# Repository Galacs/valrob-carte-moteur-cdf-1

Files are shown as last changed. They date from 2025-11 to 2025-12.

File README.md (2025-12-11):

# Carte moteur CDF 1

ESP32-S3-WROOM-1 Dual 5A DC motor driver

## IC List

- ESP32-S3-WROOM-1 (Main MCU Module)
- AP2112K (MCU 3v3 LDO)
- DRV8874 (Integrated FETs H-bridge)

## Top preview



## Preview 3d render



## Pin definitions

```c
#define EN_1_PIN 2
#define PH_1_PIN 3
#define SLEEP_1_PIN 5
#define FAULT_1_PIN 6
#define IPROPRI_1_PIN 7

#define EN_2_PIN 14
#define PH_2_PIN 17
#define SLEEP_2_PIN 21
#define FAULT_2_PIN 38
#define IPROPRI_2_PIN 18

#define SPI_CS_0_PIN 10
#define SPI_CS_1_PIN 8
#define SPI_MOSI_PIN 11
#define SPI_MISO_PIN 13
#define SPI_SCLK_PIN 12

#define ALERT_1_PIN 47
#define ALERT_2_PIN 48

#define BATT_SENSE_PIN 9
```

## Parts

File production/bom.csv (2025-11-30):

Designator | Footprint | Quantity | Value | LCSC Part #
_2, |  | 2
C1, C2, C5 | 0603 | 3 | 1u | C15849
C10, C13, C14, C4, C7, C9 | 0603 | 6 | 0u1 | C14663
C11, C15 | CP_Elec_6.3x7.7 | 2 | 220u | C46550411
C12, C8 | 0603 | 2 | 22n | C21122
C3 | 0603 | 1 | 10u | C19702
C6 | 0805 | 1 | 22u | C45783
D1, D16 | D_SMA | 2 | D_Schottky | C22452
D10, D11, D12, D13, D14, D15, D17, D18, D19, D6, D7, D8, D9 | Diode_DFN1006 | 13 | H5VU10U | C22395519
D2 | 0805 | 1 | GREEN | C2297
D3 | D_SMB | 1 | P6SMB6.8CA/TR13 | C78395
D4 | D_SOD-123 | 1 | BZT52B3V3 | C19077392
D5 | D_SMA | 1 | SMAJ12A | C19077531
J1 | USB_C_Receptacle_HRO_TYPE-C-31-M-12 | 1 | USB_C_Receptacle_USB2.0_14P | C393939
R1, R10, R15, R2, R3 | 0603 | 5 | 5k1 | C23186
R11, R16 | 0805 | 2 | 16k | C17490
R12, R17 | 0603 | 2 | 1k | C21190
R13, R18, R5, R6, R7 | 0603 | 5 | 10k | C25804
R14, R19 | 0603 | 2 | 20k | C4184
R4 | 0603 | 1 | 3k3 | C22978
R8, R9 | 0603 | 2 | 22 | C23345
SW1, SW2 | SW_SPST_TS-1088-xR020 | 2 | SW_Push | C720477
U1 | SOT-23-5 | 1 | AP2112K-3.3 | C51118
U4, U5 | HTSSOP-16-1EP_4.4x5mm_P0.65mm_EP3.4x5mm_Mask2.46x2.31mm_ThermalVias | 2 | DRV8874 | C1855818

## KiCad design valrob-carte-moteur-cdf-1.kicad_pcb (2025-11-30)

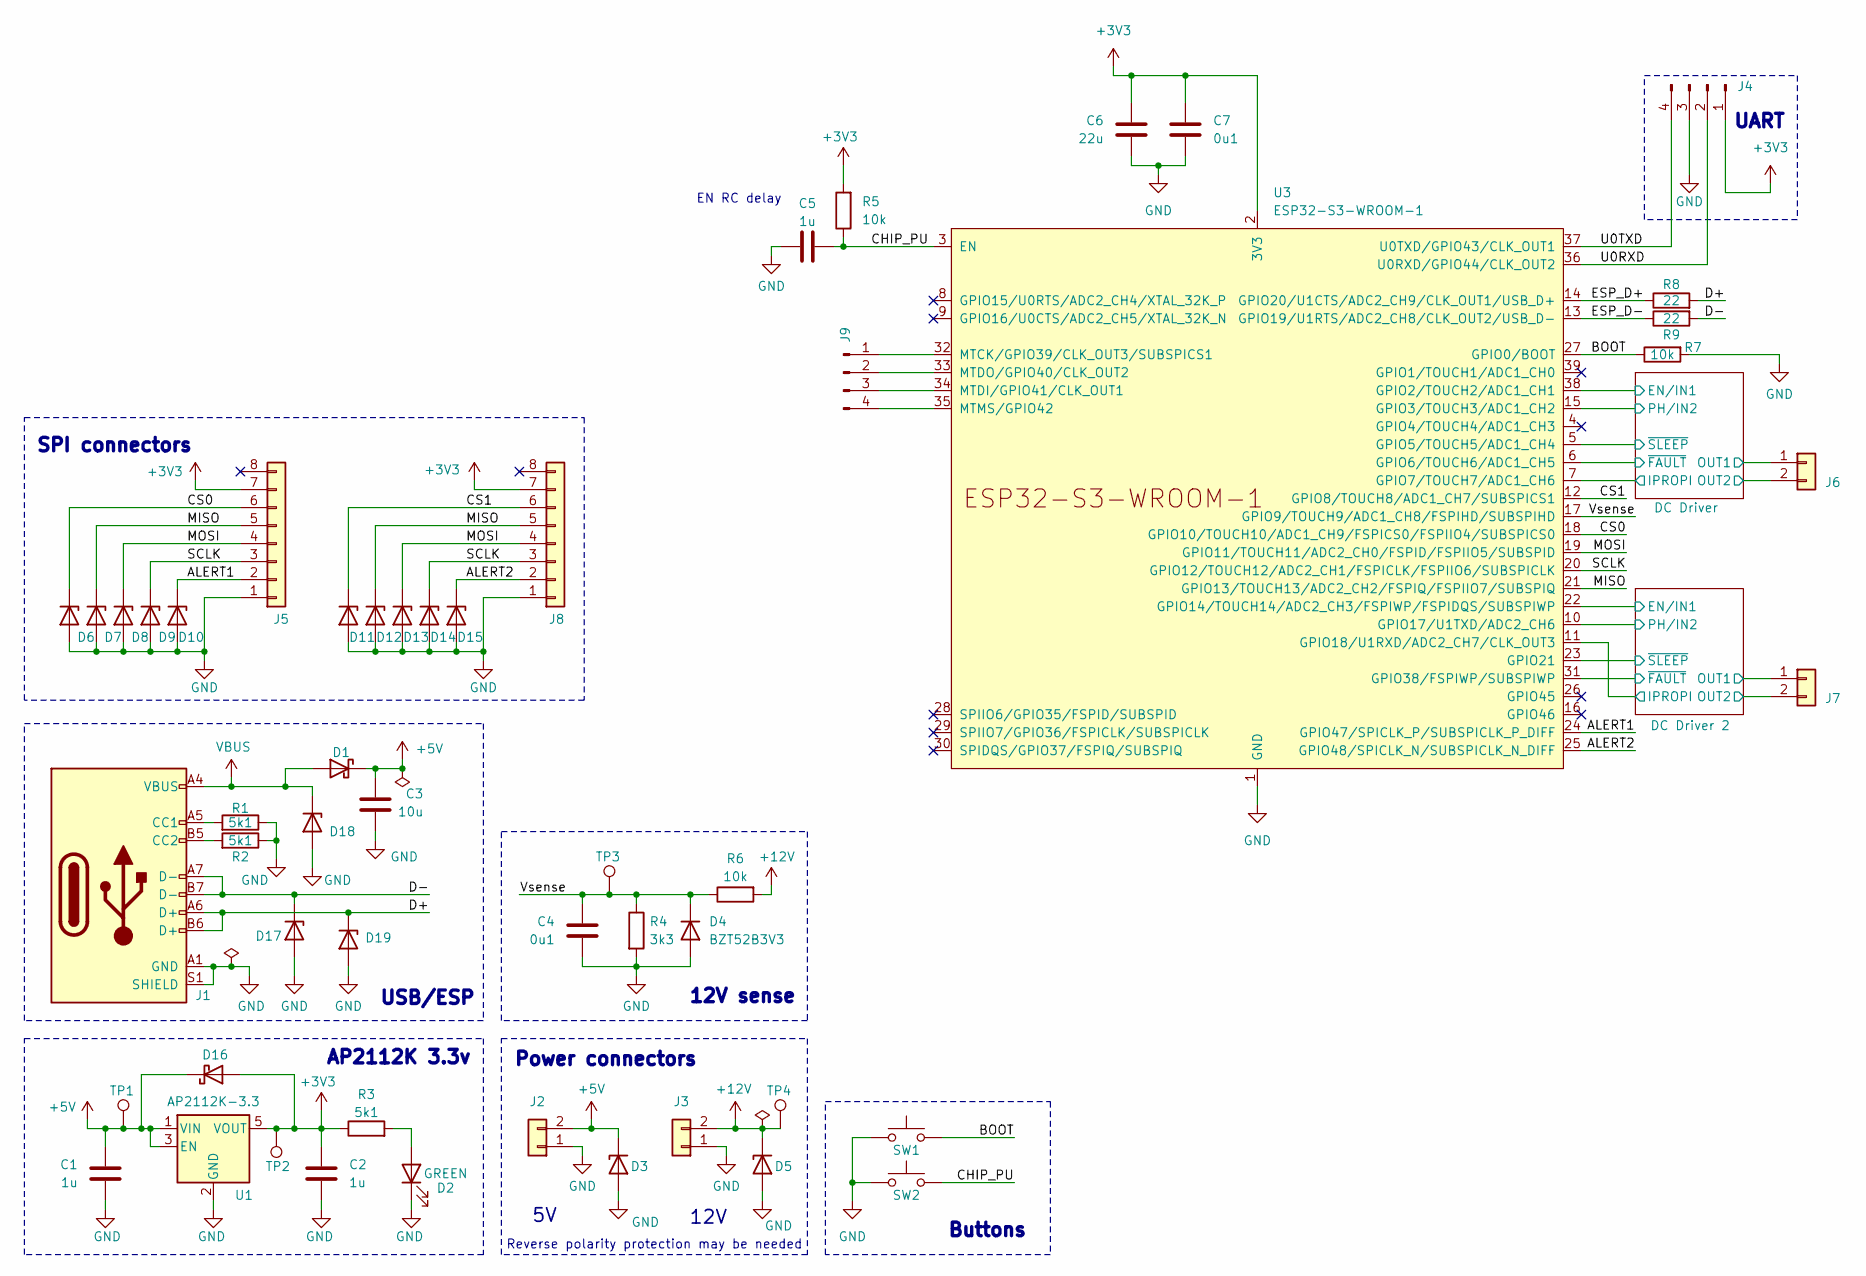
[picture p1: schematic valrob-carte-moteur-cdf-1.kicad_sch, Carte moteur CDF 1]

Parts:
C1, C2, C5: 1u; C_0603_1608Metric; Manufacturer Part Number CL10A105KB8NNNC; JLCPCB Part # C15849
C3: 10u; C_0603_1608Metric; Manufacturer Part Number CL10A106KP8NNNC; JLCPCB Part # C19702
C4, C7: 0u1; C_0603_1608Metric; Manufacturer Part Number CC0603KRX7R9BB104; JLCPCB Part # C14663
C6: 22u; C_0805_2012Metric; Manufacturer Part Number CL21A226MAQNNNE; JLCPCB Part # C45783
D1, D16: D_Schottky; D_SMA; Manufacturer Part Number SS54; JLCPCB Part # C22452
D2: GREEN; LED_0805_2012Metric; Manufacturer Part Number KT-0805G; JLCPCB Part # C2297
D3: P6SMB6.8CA/TR13; D_SMB; Manufacturer Part Number P6SMB6.8CA/TR13; JLCPCB Part # C78395
D4: BZT52B3V3; D_SOD-123; Manufacturer Part Number BZT52B3V3; JLCPCB Part # C19077392
D5: SMAJ12A; D_SMA; Manufacturer Part Number SMAJ12A; JLCPCB Part # C19077531
D6, D7, D8, D9, D10, D11, D12, D13, D14, D15, D17, D18, D19: H5VU10U; Diode_DFN1006; Manufacturer Part Number H5VU10U; JLCPCB Part # C22395519
J1: USB_C_Receptacle_USB2.0_14P; USB_C_Receptacle_HRO_TYPE-C-31-M-12; Manufacturer Part Number TYPE-C16PIN; JLCPCB Part # C393939
J2, J3, J6, J7: Conn_01x02; JST_XH_S2B-XH-A_1x02_P2.50mm_Horizontal
J4, J9: Conn_01x04_Pin; PinHeader_1x04_P2.54mm_Vertical
J5, J8: Conn_01x08; Molex_PicoBlade_53048-0810_1x08_P1.25mm_Horizontal
R1, R2, R3: 5k1; R_0603_1608Metric; Manufacturer Part Number 0603WAF5101T5E; JLCPCB Part # C23186
R4: 3k3; R_0603_1608Metric; Manufacturer Part Number 0603WAF3301T5E; JLCPCB Part # C22978
R5, R6, R7: 10k; R_0603_1608Metric; Manufacturer Part Number 0603WAF1002T5E; JLCPCB Part # C25804
R8, R9: 22; R_0603_1608Metric; Manufacturer Part Number 0603WAF220JT5E; JLCPCB Part # C23345
SW1, SW2: SW_Push; SW_SPST_TS-1088-xR020; Manufacturer Part Number TS-1088-AR02016; JLCPCB Part # C720477
TP1, TP2, TP3, TP4: TestPoint; TestPoint_Pad_D2.0mm
U1: AP2112K-3.3; SOT-23-5; Manufacturer Part Number AP2112K-3.3TRG1; JLCPCB Part # C51118
U3: ESP32-S3-WROOM-1

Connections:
+3V3: C2.1, C6.1, C7.1, D16.2 (A), J4.1, J5.7, J8.7, R3.1, R5.2, TP2.1, U1.5 (VOUT), U3.2 (3V3); also elsewhere on the board
+5V: C1.1, C3.1, D1.1 (K), D3.1 (K), D16.1 (K), J2.2, TP1.1, U1.1 (VIN), U1.3 (EN)
+12V: D5.1 (K), J3.2, R6.2, TP4.1; also elsewhere on the board
/ALERT1: D10.1 (K), J5.2, U3.24 (GPIO47/SPICLK_P/SUBSPICLK_P_DIFF)
/ALERT2: D15.1 (K), J8.2, U3.25 (GPIO48/SPICLK_N/SUBSPICLK_N_DIFF)
/BOOT: R7.1, SW1.2, U3.27 (GPIO0/BOOT)
/CHIP_PU: C5.2, R5.1, SW2.2, U3.3 (EN)
/CS0: D6.1 (K), J5.6, U3.18 (GPIO10/TOUCH10/ADC1_CH9/FSPICS0/FSPIIO4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)
/CS1: D11.1 (K), J8.6, U3.12 (GPIO8/TOUCH8/ADC1_CH7/SUBSPICS1)
/D+: D19.1 (K), J1.A6 (D+), J1.B6 (D+), R8.2
/D-: D17.1 (K), J1.A7 (D-), J1.B7 (D-), R9.2
/DC Driver 2/EN/IN1: U3.22 (GPIO14/TOUCH14/ADC2_CH3/FSPIWP/FSPIDQS/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); also elsewhere on the board
/DC Driver 2/IPROPI: U3.11 (GPIO18/U1RXD/ADC2_CH7/CLK_OUT3); also elsewhere on the board
/DC Driver 2/OUT1: J7.1; also elsewhere on the board
/DC Driver 2/OUT2: J7.2; also elsewhere on the board
/DC Driver 2/PH/IN2: U3.10 (GPIO17/U1TXD/ADC2_CH6); also elsewhere on the board
/DC Driver 2/~FAULT: U3.31 (GPIO38/FSPIWP/SUBSPIWP); also elsewhere on the board
/DC Driver 2/~SLEEP: U3.23 (GPIO21); also elsewhere on the board
/DC Driver/EN/IN1: U3.38 (GPIO2/TOUCH2/ADC1_CH1); also elsewhere on the board
/DC Driver/IPROPI: U3.7 (GPIO7/TOUCH7/ADC1_CH6); also elsewhere on the board
/DC Driver/OUT1: J6.1; also elsewhere on the board
/DC Driver/OUT2: J6.2; also elsewhere on the board
/DC Driver/PH/IN2: U3.15 (GPIO3/TOUCH3/ADC1_CH2); also elsewhere on the board
/DC Driver/~FAULT: U3.6 (GPIO6/TOUCH6/ADC1_CH5); also elsewhere on the board
/DC Driver/~SLEEP: U3.5 (GPIO5/TOUCH5/ADC1_CH4); also elsewhere on the board
/ESP_D+: R8.1, U3.14 (GPIO20/U1CTS/ADC2_CH9/CLK_OUT1/USB_D+)
/ESP_D-: R9.1, U3.13 (GPIO19/U1RTS/ADC2_CH8/CLK_OUT2/USB_D-)
/MISO: D7.1 (K), D12.1 (K), J5.5, J8.5, U3.21 (GPIO13/TOUCH13/ADC2_CH2/FSPIQ/FSPIIO7/S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)
/MOSI: D8.1 (K), D13.1 (K), J5.4, J8.4, U3.19 (GPIO11/TOUCH11/ADC2_CH0/FSPID/FSPIIO5/S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)
/SCLK: D9.1 (K), D14.1 (K), J5.3, J8.3, U3.20 (GPIO12/TOUCH12/ADC2_CH1/FSPICLK/FSPIIO6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)
/U0RXD: J4.2, U3.36 (U0RXD/GPIO44/CLK_OUT2)
/U0TXD: J4.4, U3.37 (U0TXD/GPIO43/CLK_OUT1)
/Vsense: C4.1, D4.1 (K), R4.1, R6.1, TP3.1, U3.17 (GPIO9/TOUCH9/ADC1_CH8/FSPIHD/SUBSPIHD)
GND: C1.2, C2.2, C3.2, C4.2, C5.1, C6.2, C7.2, D2.1 (K), D3.2 (A), D4.2 (A), D5.2 (A), D6.2 (A), D7.2 (A), D8.2 (A), D9.2 (A), D10.2 (A), D11.2 (A), D12.2 (A), D13.2 (A), D14.2 (A), D15.2 (A), D17.2 (A), D18.2 (A), D19.2 (A), J1.A1 (GND), J1.A12 (GND), J1.B1 (GND), J1.B12 (GND), J1.S1 (SHIELD), J2.1, J3.1, J4.3, J5.1, J8.1, R1.1, R2.1, R4.2, R7.2, SW1.1, SW2.1, U1.2 (GND), U3.1 (GND), U3.40 (GND), U3.41 (GND); also elsewhere on the board
unnamed: D2.2 (A), R3.2
unnamed: J1.A5 (CC1), R1.2
unnamed: J1.B5 (CC2), R2.2
unnamed: J9.1, U3.32 (MTCK/GPIO39/CLK_OUT3/SUBSPICS1)
unnamed: J9.2, U3.33 (MTDO/GPIO40/CLK_OUT2)
unnamed: J9.3, U3.34 (MTDI/GPIO41/CLK_OUT1)
unnamed: J9.4, U3.35 (MTMS/GPIO42)
VBUS: D1.2 (A), D18.1 (K), J1.A4 (VBUS), J1.A9 (VBUS), J1.B4 (VBUS), J1.B9 (VBUS)

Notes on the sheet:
SPI connectors
12V sense
Power connectors
Reverse polarity protection may be needed
AP2112K 3.3v
USB/ESP
Buttons
12V
UART
EN RC delay

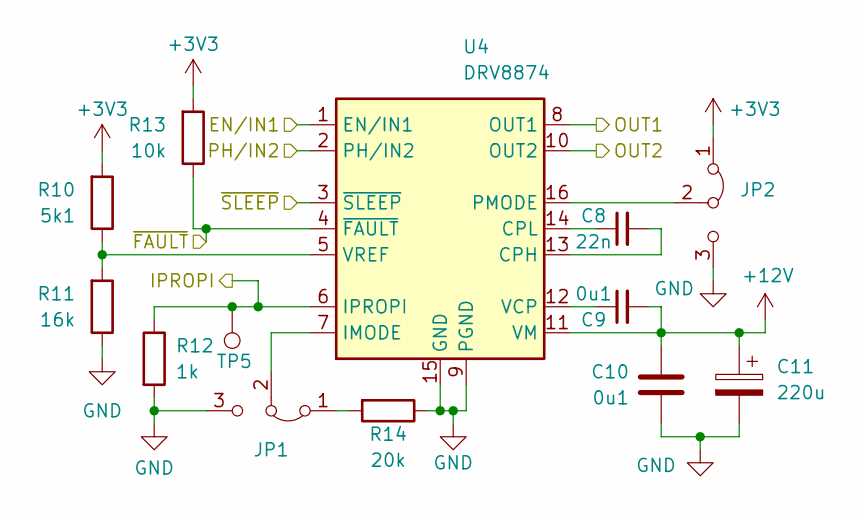
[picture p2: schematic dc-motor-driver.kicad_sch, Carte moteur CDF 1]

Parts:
C8: 22n; C_0603_1608Metric; Manufacturer Part Number CL10B223KB8NNNC; JLCPCB Part # C21122
C9, C10: 0u1; C_0603_1608Metric; Manufacturer Part Number CC0603KRX7R9BB104; JLCPCB Part # C14663
C11: 220u; CP_Elec_6.3x7.7; Manufacturer Part Number JVJ35V220M6x8; JLCPCB Part # C46550411
JP1, JP2: Jumper_3_Bridged12; PinHeader_1x03_P2.54mm_Vertical
R10: 5k1; R_0603_1608Metric; Manufacturer Part Number 0603WAF5101T5E; JLCPCB Part # C23186
R11: 16k; R_0805_2012Metric; Manufacturer Part Number 0805W8F1602T5E; JLCPCB Part # C17490
R12: 1k; R_0603_1608Metric; Manufacturer Part Number 0603WAF1001T5E; JLCPCB Part # C21190
R13: 10k; R_0603_1608Metric; Manufacturer Part Number 0603WAF1002T5E; JLCPCB Part # C25804
R14: 20k; R_0603_1608Metric; Manufacturer Part Number 0603WAF2002T5E; JLCPCB Part # C4184
TP5: TestPoint; TestPoint_Pad_D2.0mm
U4: DRV8874; HTSSOP-16-1EP_4.4x5mm_P0.65mm_EP3.4x5mm_Mask2.46x2.31mm_The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; Manufacturer Part Number DRV8874PWPR; JLCPCB Part # C1855818

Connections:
+3V3: JP2.1 (A), R10.2, R13.2; also elsewhere on the board
+12V: C9.2, C10.1, C11.1, U4.11 (VM); also elsewhere on the board
/DC Driver/EN/IN1: U4.1 (EN/IN1); also elsewhere on the board
/DC Driver/IPROPI: R12.1, TP5.1, U4.6 (IPROPI); also elsewhere on the board
/DC Driver/OUT1: U4.8 (OUT1); also elsewhere on the board
/DC Driver/OUT2: U4.10 (OUT2); also elsewhere on the board
/DC Driver/PH/IN2: U4.2 (PH/IN2); also elsewhere on the board
/DC Driver/~FAULT: R13.1, U4.4 (~FAULT); also elsewhere on the board
/DC Driver/~SLEEP: U4.3 (~SLEEP); also elsewhere on the board
GND: C10.2, C11.2, JP1.3 (B), JP2.3 (B), R11.1, R12.2, R14.1, U4.9 (PGND), U4.15 (GND); also elsewhere on the board
unnamed: JP1.1 (A), R14.2
unnamed: JP1.2 (C), U4.7 (IMODE)
unnamed: JP2.2 (C), U4.16 (PMODE)
unnamed: C8.2, U4.13 (CPH)
unnamed: C8.1, U4.14 (CPL)
unnamed: C9.1, U4.12 (VCP)
unnamed: R10.1, R11.2, U4.5 (VREF)

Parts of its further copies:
C12: 22n; C_0603_1608Metric; Manufacturer Part Number CL10B223KB8NNNC; JLCPCB Part # C21122
C13, C14: 0u1; C_0603_1608Metric; Manufacturer Part Number CC0603KRX7R9BB104; JLCPCB Part # C14663
C15: 220u; CP_Elec_6.3x7.7; Manufacturer Part Number JVJ35V220M6x8; JLCPCB Part # C46550411
JP3, JP4: Jumper_3_Bridged12; PinHeader_1x03_P2.54mm_Vertical
R15: 5k1; R_0603_1608Metric; Manufacturer Part Number 0603WAF5101T5E; JLCPCB Part # C23186
R16: 16k; R_0805_2012Metric; Manufacturer Part Number 0805W8F1602T5E; JLCPCB Part # C17490
R17: 1k; R_0603_1608Metric; Manufacturer Part Number 0603WAF1001T5E; JLCPCB Part # C21190
R18: 10k; R_0603_1608Metric; Manufacturer Part Number 0603WAF1002T5E; JLCPCB Part # C25804
R19: 20k; R_0603_1608Metric; Manufacturer Part Number 0603WAF2002T5E; JLCPCB Part # C4184
TP6: TestPoint; TestPoint_Pad_D2.0mm
U5: DRV8874; HTSSOP-16-1EP_4.4x5mm_P0.65mm_EP3.4x5mm_Mask2.46x2.31mm_The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; Manufacturer Part Number DRV8874PWPR; JLCPCB Part # C1855818

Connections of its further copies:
+3V3: JP4.1 (A), R15.2, R18.2; also elsewhere on the board
+12V: C13.2, C14.1, C15.1, U5.11 (VM); also elsewhere on the board
/DC Driver 2/EN/IN1: U5.1 (EN/IN1); also elsewhere on the board
/DC Driver 2/IPROPI: R17.1, TP6.1, U5.6 (IPROPI); also elsewhere on the board
/DC Driver 2/OUT1: U5.8 (OUT1); also elsewhere on the board
/DC Driver 2/OUT2: U5.10 (OUT2); also elsewhere on the board
/DC Driver 2/PH/IN2: U5.2 (PH/IN2); also elsewhere on the board
/DC Driver 2/~FAULT: R18.1, U5.4 (~FAULT); also elsewhere on the board
/DC Driver 2/~SLEEP: U5.3 (~SLEEP); also elsewhere on the board
GND: C14.2, C15.2, JP3.3 (B), JP4.3 (B), R16.1, R17.2, R19.1, U5.9 (PGND), U5.15 (GND); also elsewhere on the board
unnamed: JP3.1 (A), R19.2
unnamed: JP3.2 (C), U5.7 (IMODE)
unnamed: JP4.2 (C), U5.16 (PMODE)
unnamed: C12.2, U5.13 (CPH)
unnamed: C12.1, U5.14 (CPL)
unnamed: C13.1, U5.12 (VCP)
unnamed: R15.1, R16.2, U5.5 (VREF)

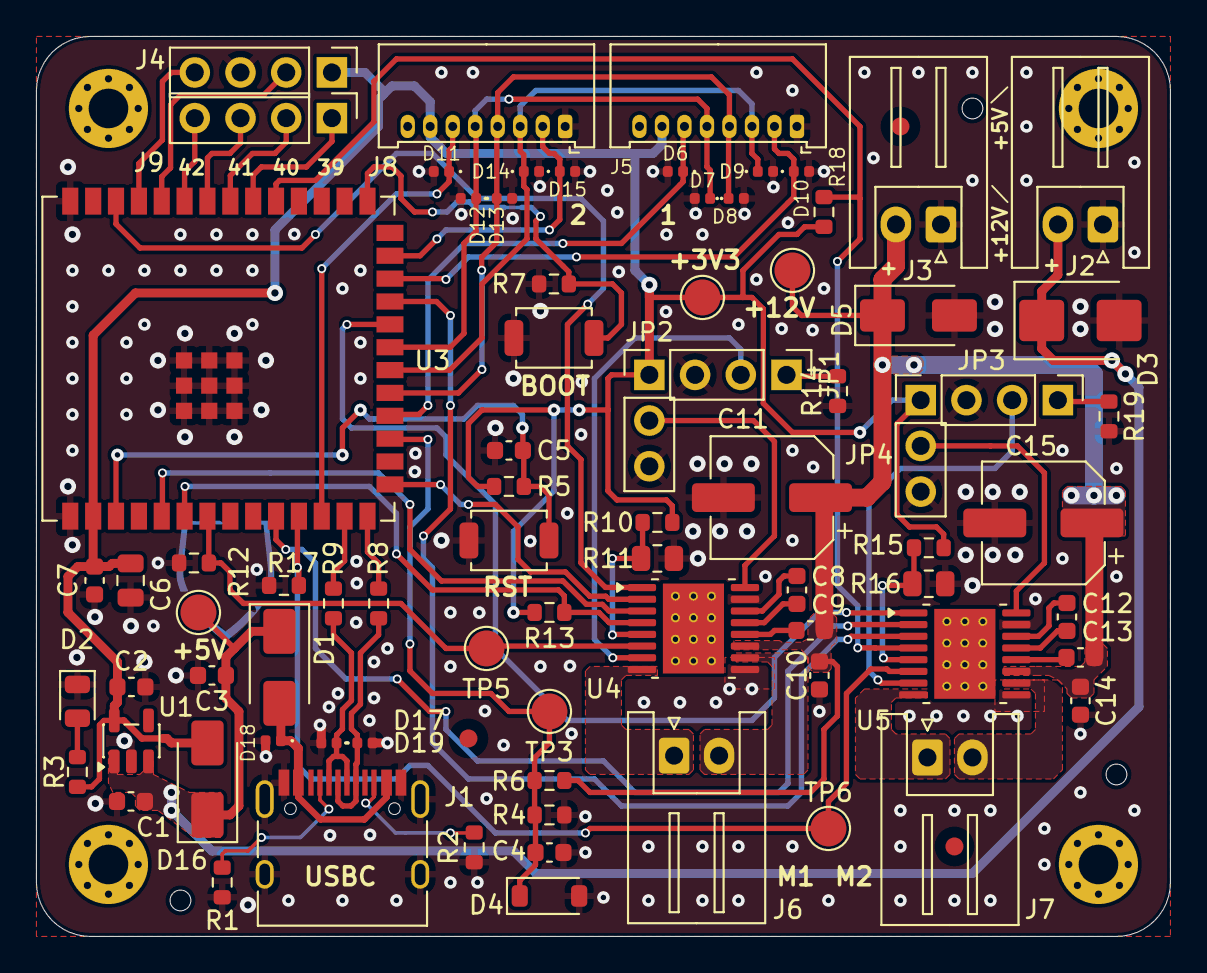
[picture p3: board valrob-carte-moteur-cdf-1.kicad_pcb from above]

Board: 2 copper layers, 63.0 x 50.0 mm, 78 parts (0 on the bottom side), 56 nets.

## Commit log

2025-11-23 schem: add ESP32-S3-WROOM-1 symbol
    [valrob-carte-moteur-cdf-1.kicad_sch]
2025-11-23 schem: add ESP32 decoupling caps
    [valrob-carte-moteur-cdf-1.kicad_sch]
2025-11-23 schem: import AP2112K 3.3v from esp32c6-sensor-devboard
    [valrob-carte-moteur-cdf-1.kicad_sch]
2025-11-23 schem: import USB-C from esp32c6-sensor-devboard
    [valrob-carte-moteur-cdf-1.kicad_sch]
2025-11-23 schem: add BOOT and CHIP_PU strapping pullups
    [valrob-carte-moteur-cdf-1.kicad_sch]
2025-11-23 schem: import boot and rst btns from esp32c6-sensor-devboard
    [valrob-carte-moteur-cdf-1.kicad_sch]
2025-11-23 schem: import UART connector without series resistor from esp32c6-sensor-devboard
    [valrob-carte-moteur-cdf-1.kicad_sch]
2025-11-23 schem: add USB termination resistors
    [valrob-carte-moteur-cdf-1.kicad_sch]
2025-11-23 schem: add power 5v and 12v power input connectors
    [valrob-carte-moteur-cdf-1.kicad_sch]
2025-11-23 schem: add 12v sense from MCU ADC or GPIO
    [valrob-carte-moteur-cdf-1.kicad_sch]
2025-11-23 schem: add ESD/Surge protection to power inputs
    [valrob-carte-moteur-cdf-1.kicad_sch]
2025-11-23 schem: add SPI connectors
    [valrob-carte-moteur-cdf-1.kicad_sch]
2025-11-23 schem: add DRV8874 dc motor driver
    [dc-motor-driver.kicad_sch, valrob-carte-moteur-cdf-1.kicad_sch]
2025-11-23 schem: add second dc motor driver
    [dc-motor-driver.kicad_sch, valrob-carte-moteur-cdf-1.kicad_sch]
2025-11-23 schem: connect SPI connectors to ESP32S3
    [dc-motor-driver.kicad_sch, valrob-carte-moteur-cdf-1.kicad_sch]
2025-11-23 schem: add various test points
    [dc-motor-driver.kicad_sch, valrob-carte-moteur-cdf-1.kicad_sch]
2025-11-23 schem: add no connects to unused ESP32 pins
    [valrob-carte-moteur-cdf-1.kicad_sch]
2025-11-23 schem: connect alert pins to ESP32
    [valrob-carte-moteur-cdf-1.kicad_sch]
2025-11-23 schem: reannotate
    [dc-motor-driver.kicad_sch, valrob-carte-moteur-cdf-1.kicad_sch]
2025-11-23 schem: run and fix ERC
    [dc-motor-driver.kicad_sch, valrob-carte-moteur-cdf-1.kicad_sch]
2025-11-23 schem: add sheet titles
    [dc-motor-driver.kicad_sch, valrob-carte-moteur-cdf-1.kicad_sch]
2025-11-23 schem: reorganize layout
    [valrob-carte-moteur-cdf-1.kicad_sch]
2025-11-23 schem: add components footprints
    [dc-motor-driver.kicad_sch, valrob-carte-moteur-cdf-1.kicad_sch]
2025-11-23 schem: add ordering info to BOM
    [dc-motor-driver.kicad_sch, valrob-carte-moteur-cdf-1.kicad_sch]
2025-11-23 pcb: create file
    [valrob-carte-moteur-cdf-1.kicad_pcb]
2025-11-23 pcb: import stackup and constraints
    [valrob-carte-moteur-cdf-1.kicad_pcb]
2025-11-23 pcb: switch stackup to 2 layers
    [valrob-carte-moteur-cdf-1.kicad_pcb]
2025-11-23 pcb: import footprints from schematic
    [valrob-carte-moteur-cdf-1.kicad_pcb]
2025-11-23 pcb: add missing 3d models
    [valrob-carte-moteur-cdf-1.kicad_pcb]
2025-11-23 pcb: initial rough placement
    [valrob-carte-moteur-cdf-1.kicad_pcb]
2025-11-23 schem: add ldo reverse current protection diode
    [valrob-carte-moteur-cdf-1.kicad_sch]
2025-11-23 pcb: add 4 M2 mounting holes
    [valrob-carte-moteur-cdf-1.kicad_pcb]
2025-11-23 pcb: add fiducials and tooling holes
    [valrob-carte-moteur-cdf-1.kicad_pcb]
2025-11-23 pcb: layout refinement
    [valrob-carte-moteur-cdf-1.kicad_pcb]
2025-11-23 pcb: add gnd planes
    [valrob-carte-moteur-cdf-1.kicad_pcb]
2025-11-23 pcb: add ground vias
    [valrob-carte-moteur-cdf-1.kicad_pcb]
2025-11-23 pcb: add usb routing
    [valrob-carte-moteur-cdf-1.kicad_pcb]
2025-11-23 pcb: add SPI routing
    [valrob-carte-moteur-cdf-1.kicad_pcb]
2025-11-23 pcb: add uart routing
    [valrob-carte-moteur-cdf-1.kicad_pcb]
2025-11-23 pcb: add DRV8874 dc motor driver routing
    [valrob-carte-moteur-cdf-1.kicad_pcb, valrob-carte-moteur-cdf-1.kicad_sch]
2025-11-23 pcb: add 12V routing
    [valrob-carte-moteur-cdf-1.kicad_pcb]
2025-11-23 pcb: route power
    [valrob-carte-moteur-cdf-1.kicad_pcb]
2025-11-23 pcb: add CHIP_PU AND BOOT routing
    [valrob-carte-moteur-cdf-1.kicad_pcb]
2025-11-23 pcb(silkscreen): clean reference designators
    [valrob-carte-moteur-cdf-1.kicad_pcb]
2025-11-23 pcb: add stitching vias
    [valrob-carte-moteur-cdf-1.kicad_pcb]
2025-11-23 pcb: run and fix DRC
    [valrob-carte-moteur-cdf-1.kicad_pcb]
2025-11-23 pcb: remove unused internal pads
    [valrob-carte-moteur-cdf-1.kicad_pcb]
2025-11-23 pcb: add title
    [valrob-carte-moteur-cdf-1.kicad_pcb]
2025-11-23 pcb: add silkscreen bling
    [valrob-carte-moteur-cdf-1.kicad_pcb]
2025-11-23 add spare gpios
    [valrob-carte-moteur-cdf-1.kicad_pcb, valrob-carte-moteur-cdf-1.kicad_sch]
2025-11-23 pcb(silkscreen): add JLC order number placeholder
    [valrob-carte-moteur-cdf-1.kicad_pcb]
2025-11-24 pcb: add company logo to back
    [valrob-carte-moteur-cdf-1.kicad_pcb]
2025-11-25 switch ST usb ESD to H5VU10U tvs diodes
    [valrob-carte-moteur-cdf-1.kicad_pcb, valrob-carte-moteur-cdf-1.kicad_sch]
2025-11-25 pcb(silkscreeen): improvements
    [valrob-carte-moteur-cdf-1.kicad_pcb, valrob-carte-moteur-cdf-1.kicad_sch]
2025-11-25 fix spi connectors TVS diodes polarity
    [valrob-carte-moteur-cdf-1.kicad_pcb, valrob-carte-moteur-cdf-1.kicad_sch]
2025-11-25 schem: fix batt sense
    [valrob-carte-moteur-cdf-1.kicad_pcb, valrob-carte-moteur-cdf-1.kicad_sch]
2025-11-30 bom: change dc driver bulk capacitors P#
    [dc-motor-driver.kicad_sch, valrob-carte-moteur-cdf-1.kicad_pcb]
2025-11-30 regenerate production files
    [bom.csv, designators.csv, positions.csv]
2025-12-05 docs: add pin definitions to readme
